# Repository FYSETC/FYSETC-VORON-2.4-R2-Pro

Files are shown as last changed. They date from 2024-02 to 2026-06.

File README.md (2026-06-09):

# FYSETC-VORON-2.4-R2-Pro



## 1. Project

This is FYSETC's project database for VORON 2.4 R2 kit, which is convenient for you to find information. Thanks for VORON Team's great work, they always design fantastic printers.

Official website:：https://vorondesign.com/voron2.4
Official Github：https://github.com/VoronDesign/Voron-2/tree/V2.4r2

In folder `Voron-2-Voron2.4` beside this README file, we make some small changes base on the VORON official material. Like change the board to Spider and others. 

## 2. Fysetc Spider 3.0 H7 Spider
The latest revision of the R2 Pro kit may contain the H7 Spider board, more information on flashing this board can be found on it's official github repository here: https://github.com/FYSETC/FYSETC-SPIDER-H7 and Wiki article here: https://wiki.fysetc.com/docs/SPIDERV3H7

## 3. Fysetc SB Combo V2
The latest revision of the R2 Pro kit may contain the SB Combo V2 Toolhead board, more information on flashing this board can be found on it's official github repository here: https://github.com/FYSETC/SB_Combo_V2/tree/main and Wiki article here: https://wiki.fysetc.com/docs/SBComboV2

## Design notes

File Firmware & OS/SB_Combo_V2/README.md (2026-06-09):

Configuration for the FYSETC-VORON-2.4-R2-Pro with Fysetc SB_Combo_V2 toolhead board.

See https://wiki.fysetc.com/docs/SBComboV2 for more info on the SB Combo V2

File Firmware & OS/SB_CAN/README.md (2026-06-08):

Config for FYSETC-VORON-2.4-R2-Pro with SB_CAN toolhead board.

1. Set Spider V3.0 to  "USB to CAN bus bridge",at the "make menuconfig" command;
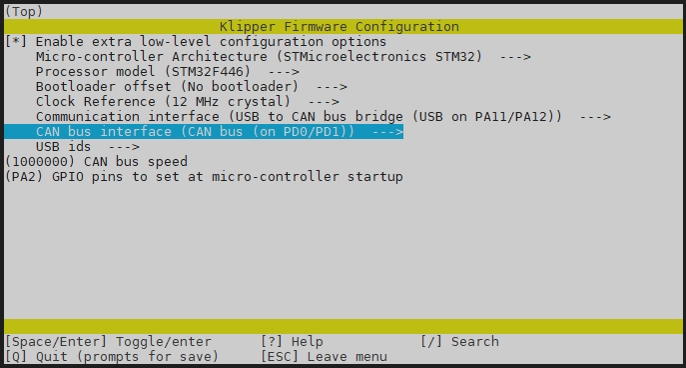
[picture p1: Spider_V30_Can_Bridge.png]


How to upload Spider V3.0 firmware?
Please refer to the following link:
https://wiki.fysetc.com/SB%20CAN%20ToolHead/#for-v13

3. Set the SB CAN V1.3 to Can bus at PB8/PB9
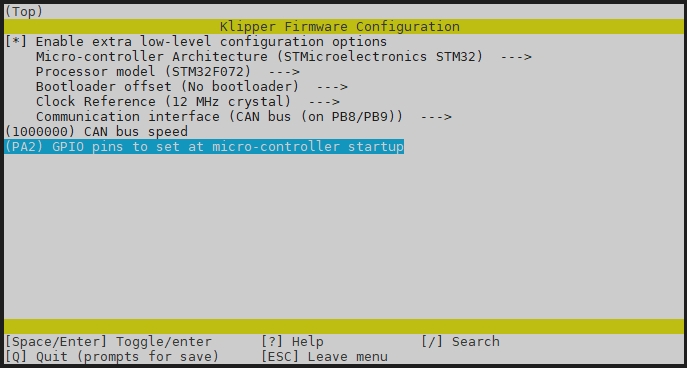
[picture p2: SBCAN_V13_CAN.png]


How to upload SB CAN V1.3 firmware?
Please refer to the following link:
https://wiki.fysetc.com/SB%20CAN%20ToolHead/#for-v13

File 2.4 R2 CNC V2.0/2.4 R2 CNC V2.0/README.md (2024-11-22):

# FYSETC-VORON-2.4-R2-Pro



## 1. Project

# VORON 2 4 R2 V2 0 Machined parts plus screws kit

Here is our video installation tutorial：

https://www.youtube.com/watch?v=xVdmxemSPT4

If you have any questions, please contact us as soon as possible

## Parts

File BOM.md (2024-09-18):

# Package list 

## VORON 2.4 R2 PRO 350 Revision 1.0

| Index | Sort | Component | Qty | Note |
| ----- | --- | --- | --- | --- |
| 1 | Fasteners | Voron V2.4 R2 fasteners Pack（12.9） | 1 SET  | |
| 2 | Motion | GATES GT2 Open Belt LL-2GT-6 (6mm wide) - 2000mm | 2 PC | |
| 3 | Motion | GATES GT2 Open Belt LL-2GT-9 (9mm wide) - 1200mm | 4 PC | |
| 4 | Motion | GATES GT2 Belt Loop (6mm W) - 188mm | 4 PCS  | |
| 5 | Motion | GT2 20T Pulley (5mm ID 6mm W) | 2 PCS  | |
| 6 | Motion | GT2 16T Pulley (5mm ID 6mm W) | 4 PCS  | |
| 7 | Motion | GT2 20T Pulley (5mm ID 9mm W) | 4 PCS  | |
| 8 | Motion | GT2 20T Toothed Idler (5mm ID 6mm W) | 2 PCS  | |
| 9 | Motion | GT2 20T Toothed Idler (5mm ID 9mm W) | 4 PCS  | |
| 10 | Motion | GT2 80T Pulley (5mm ID 6mm W) | 4 PCS  | |
| 11 | Motion | F695-2RS Bearing | 20 PCS | |
| 12 | Motion | 625 Bearing | 12 PCS | |
| 13 | Motion | 5x60mm Shaft | 4 PCS  | |
| 14 | Motion | Linear Rail MGN9H 400mm | 6 PCS  | |
| 15 | Motion | Linear Rail MGN12H Z1 400mm Light weight Stainless steel 440C | 1 PCS  | upgrade |
| 16 | Vibration Management | Rubber Compressor Foot | 4 PCS  | |
| 17 | Electronics | Stealthburner CAN Toolhead Board | 1 SET  | upgrade |
| 18 | Electronics | Stealthburner CAN Toolhead Board | 1 PC | upgrade |
| 19 | Electronics | X AXIS ENDSTOP OMRON MICROSWITCH | 1 SET  | ON extruder |
| 20 | Electronics | Y AXIS ENDSTOP OMRON MICROSWITCH | 1 SET  | Independent |
| 21 | Electronics | NeoPixel RGBW Mini Button PCB LED | 1 SET  | upgrade |
| 22 | Electronics | Omron G3NB-225B-1 SSR | 1 PC | |
| 23 | Electronics | NEMA17 Motor  17HS19-2004S-C (check [here](https://github.com/FYSETC/FYSETC-MOTORS/tree/main/17HS19-2004S-C)) | 4 PCS  | |
| 24 | Electronics | NEMA17 Motor  17HS19-2004S-AB (XY motor check [here](https://github.com/FYSETC/FYSETC-VORON-2.4-R2-Pro/tree/main/Docs/Stepper%20motor%20parameters)) | 2 PCS  | upgrade |
| 25 | Electronics | G36HSY4405-6D-60(check [here](https://github.com/FYSETC/FYSETC-VORON-2.4-R2-Pro/tree/main/Docs/Stepper%20motor%20parameters)) | 1 PC | |
| 26 | Electronics | Mean Well LRS-200-24 PSU | 1 PC | |
| 27 | Electronics | Inlet Power Socket CW2B-10A-T | 1 SET  | upgrade |
| 28 | Electronics | 40x40x10 Axial Fan (24V)  Dual Ball Bearing | 1 PC | upgrade |
| 29 | Electronics | 50x50x15 Centrifugal Fan (24V)  Dual Ball Bearing | 1 PC | upgrade |
| 30 | Electronics | 60x60x20 Fan (24V)kit（3 PCS）Dual Ball Bearing | 1 SET  | upgrade |
| 31 | Electronics | Keystone CAT6 Insert | 1 PC | |
| 32 | Electronics | C13 Power Cord | 1 PC | |
| 33 | Controller | RaspberryPi（Optional） | 1 PC | |
| 34 | Controller | sdcard 16GB | 1 PC | |
| 35 | Controller | USB C cable | 1 PC | |
| 36 | Controller | SPIDER_H7_V30 Board | 1 PC | |
| 37 | Controller | TMC2209 Stepper Motor Driver | 6 PCS  | |
| 38 | Controller | HDMI5 Display | 1 PC | upgrade |
| 39 | Frame | Light weight Gantry | 1 SET  | upgrade |
| 40 | Frame | OpenBuilds Angle Corner Connector | 4 PCS  | |
| 41 | Frame | Misumi sectional profile Kit HFSB5-2020 SET | 18 PCS | |
| 42 | Misc | PTFE Tube (4mm OD 2mm ID) - 1.5m | 1 PC | |
| 43 | Misc | 6x3mm Neodimium Magnet | 10 PCS | |
| 44 | Misc | 4mm Bowden Coupler | 1 PC | |
| 45 | Misc | BMG nano-coating one-piece helical gear kit (Includes all accessories) | 1 SET  | upgrade |
| 46 | Misc | Sailfish High Flow Hotend （ all-metal hotend 24V 60W) | 1 SET  | upgrade |
| 47 | Misc | DIN 3 Rails (35mm W) - 460mm | 2 PCS  | |
| 48 | Misc | DIN Rail Mount Bracket for G3A SSR | 1 PC | |
| 49 | Misc | Fume Extractor Carbon Filter Element | 1 PC | |
| 50 | Misc | 3M VHB Tape 5952 | 1 PC | |
| 51 | Misc | Foam Tape Thickness 1mm Length 5m | 1PC | |
| 52 | Misc | Foam Tape Thickness 3mm Length 4m | 2 PCS  | |
| 53 | Misc | XH2.54 2/3/4 Pin Plastic shell | 1 SET  | |
| 54 | Mics | Zip ties | 1 SET  | |
| 55 | Cables | Cable Kit（Pre-crimped terminals and longer wire lengths with label） | 1 SET  | |
| 56 | Cables | VORON 2.4 Chain Kit (1PC 15X10mm，XY axis cancellation) | 1 PC | Change |
| 57 | Panels | Bottom/Back/Electronics Bay Panels | 3 PCS  | |
| 58 | Panels | Side/Front/Top Acrylic Panels | 4 PCS  | |
| 59 | Buildplate | MIC6 5/16" Plate - 355X355mm （Surface milling improve flatness） | 1 PC | |
| 60 | Buildplate | Silicone AC Heater - 350x350mm (1000W)+Thermal Fuse RH15A125（Pluggable） | 1 PC | upgrade |
| 61 | Buildplate | JanusBPS Textured steel plate 355X355mm （One side pattern and the other side glossy PEI sticker） | 1 PC | [JanusBPS](https://www.google.com/search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) |
| 62 | Buildplate | Scratch-proof Magnetic stickers 355X355mm thickness 1.5mm | 1 PC | upgrade |
| 63 | Buildplate | Hotbed Insulation cotton thickness 5mm | 1 PC | upgrade |
| 64 | Tool | Cutting pliers | 1 PC | |
| 65 | Tool | Hexagonal wrenchs | 1 SET  | |
| 66 | Tool | Thermal silica | 1 PC | |
| 67 | Mics | PVC wiring duct 30x30mm | 1 SET  | |
| 68 | Mics | Wago 221-415 Terminals | 3 PCS  | |
| 69 | Mics | VORON Nevermore V6 | 1 SET  | upgrade |
| 70 | Mics | Weaving casing | 1 SET  | |
| 71 | Mics | The standby line 3m | 1 PC | |
| 72 | Mics | Wiring diagram | 1 PC | |
| 73 | Mics | VORON Hotend Cleaning brush | 1 SET  | upgrade |
| 74 | Mics | VORON Hotbed PEEK column | 1 SET  | upgrade |
| 75 | Mics | VORON CNC TAP Aluminium alloy（HIWIN） | 1 SET  | upgrade |

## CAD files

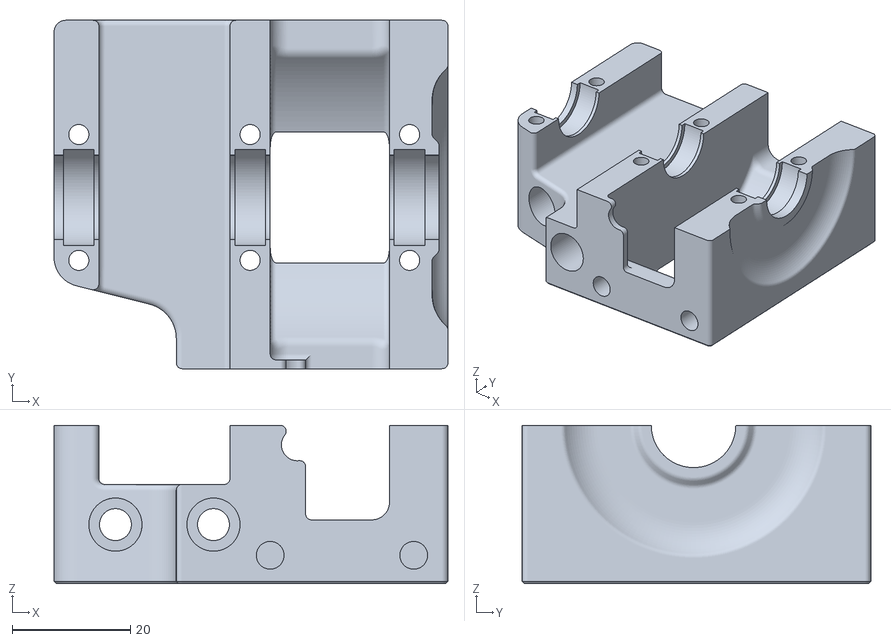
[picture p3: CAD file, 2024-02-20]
STLs/Z_Drive/z_drive_main_b_x2.stl
66.7 x 59.0 x 26.8

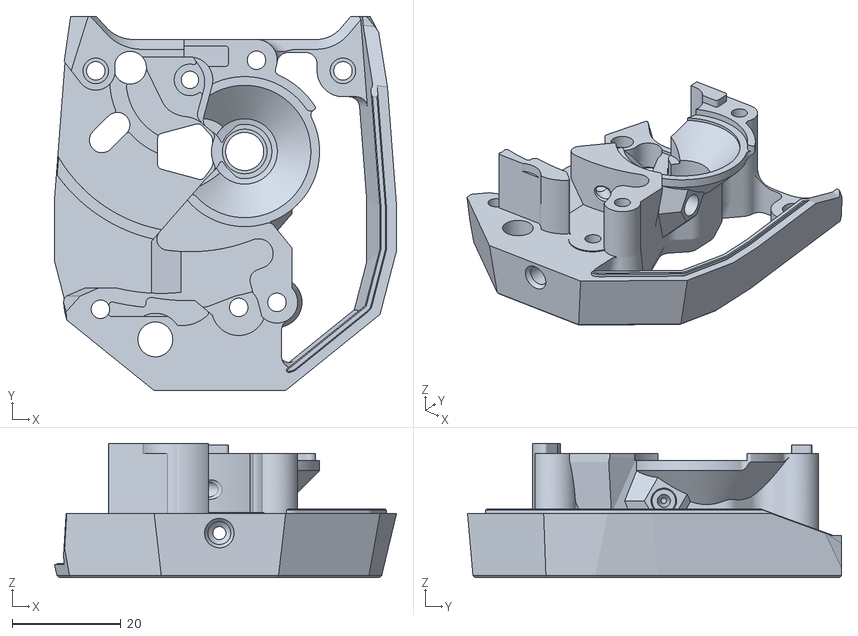
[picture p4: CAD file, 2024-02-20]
2.4 R2 CNC V2.0/2.4 R2 CNC V2.0/STL/VORON 2.4 R2 350 size V2.0 CNC SLT file/Gantry/X_Axis/X_Carriage/Voron-Stealthburner/Clockwork2/Direct_Drive/main_body.stl
62.8 x 68.7 x 24.7

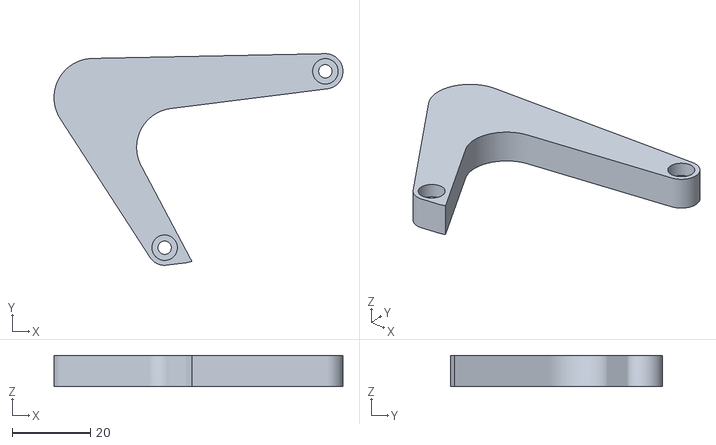
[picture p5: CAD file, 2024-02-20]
2.4 R2 CNC V2.0/2.4 R2 CNC V2.0/STL/VORON 2.4 R2 300 size V2.0 CNC SLT file/Skirts/HDMI5 Display/Five inches-Main arm B x1.STL
73.7 x 54.0 x 8.00

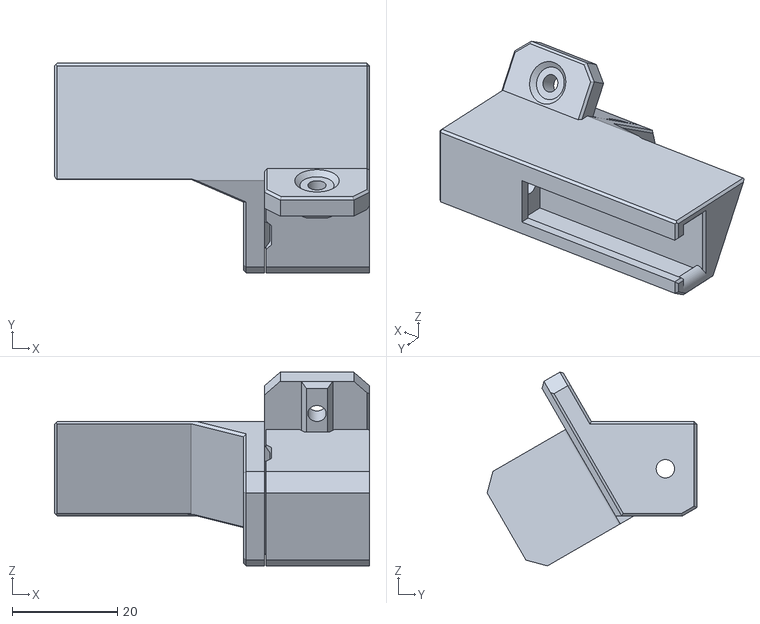
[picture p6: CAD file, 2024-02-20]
2.4 R2 CNC V2.0/2.4 R2 CNC V2.0/STL/VORON 2.4 R2 300 size V2.0 CNC SLT file/Cleaning brush/Voron R2&2.4 Cleaning brush.STL
60.0 x 39.9 x 36.9

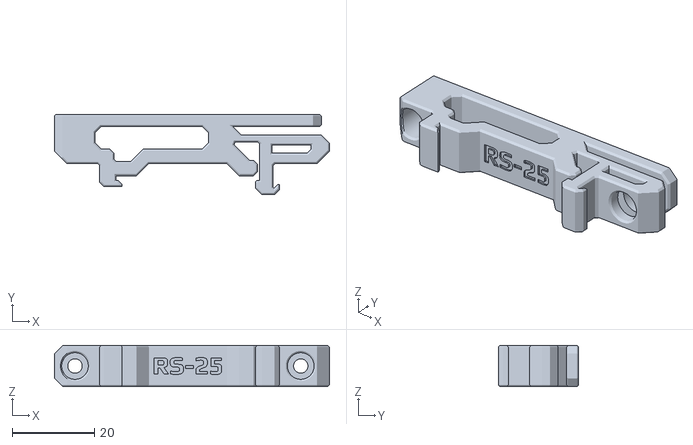
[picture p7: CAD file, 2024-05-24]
2.4 R2 CNC V2.0/2.4 R2 CNC V2.0/STL/VORON 2.4 R2 300 size V2.0 CNC SLT file/Electronics_Bay/rs25_psu_bracket.stl
67.0 x 19.6 x 10.0

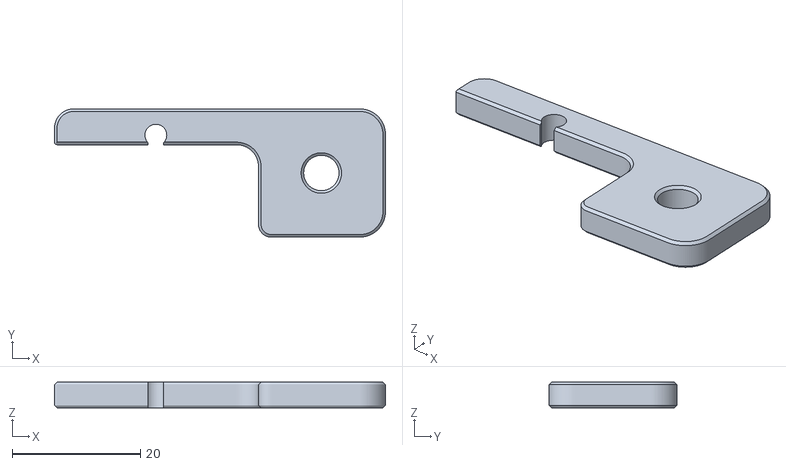
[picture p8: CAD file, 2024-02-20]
2.4 R2 CNC V2.0/2.4 R2 CNC V2.0/STL/VORON 2.4 R2 300 size V2.0 CNC SLT file/Exhaust_Filter/[a]_exhaust_filter_mount_x2.stl
51.6 x 20.0 x 4.00

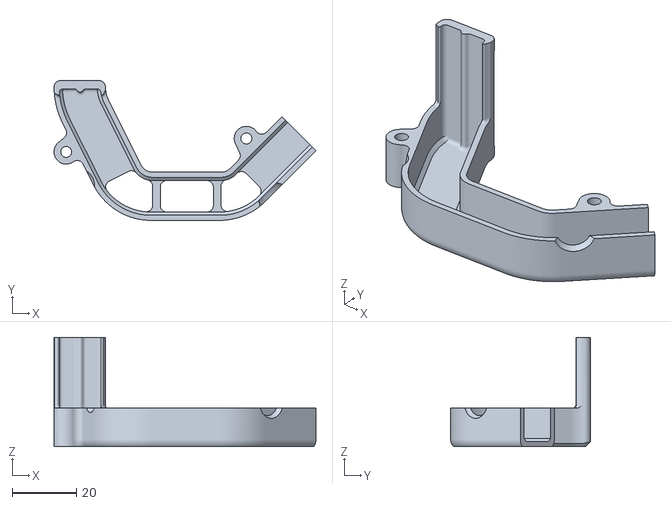
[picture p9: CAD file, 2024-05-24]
2.4 R2 CNC V2.0/2.4 R2 CNC V2.0/STL/VORON 2.4 R2 300 size V2.0 CNC SLT file/Gantry/AB_Drive_Units/[a]_cable_cover.stl
81.5 x 43.5 x 34.0

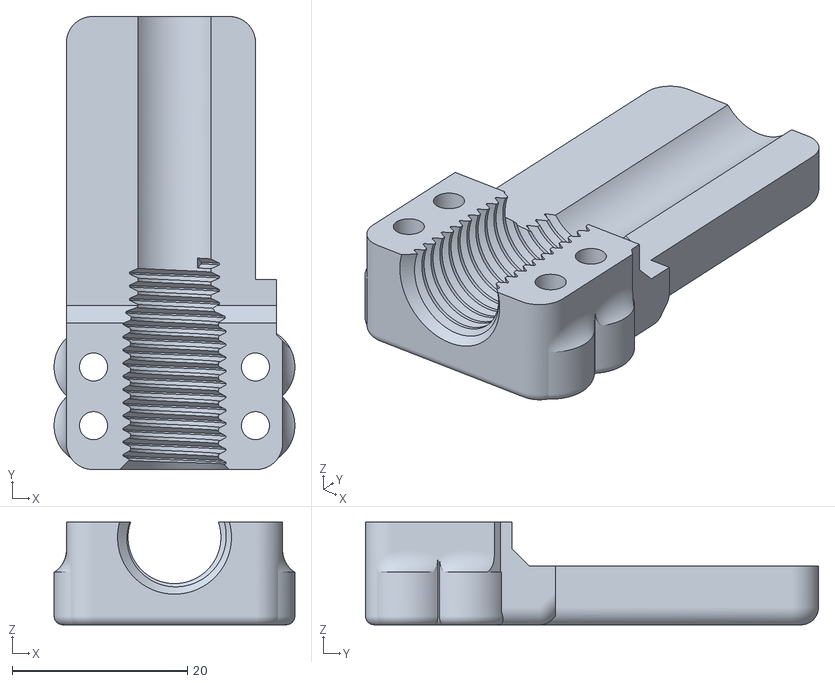
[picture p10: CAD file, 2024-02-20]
2.4 R2 CNC V2.0/2.4 R2 CNC V2.0/STL/VORON 2.4 R2 300 size V2.0 CNC SLT file/Gantry/AB_Drive_Units/Rear_Umbilical/front_cover.STL
27.5 x 51.7 x 11.7

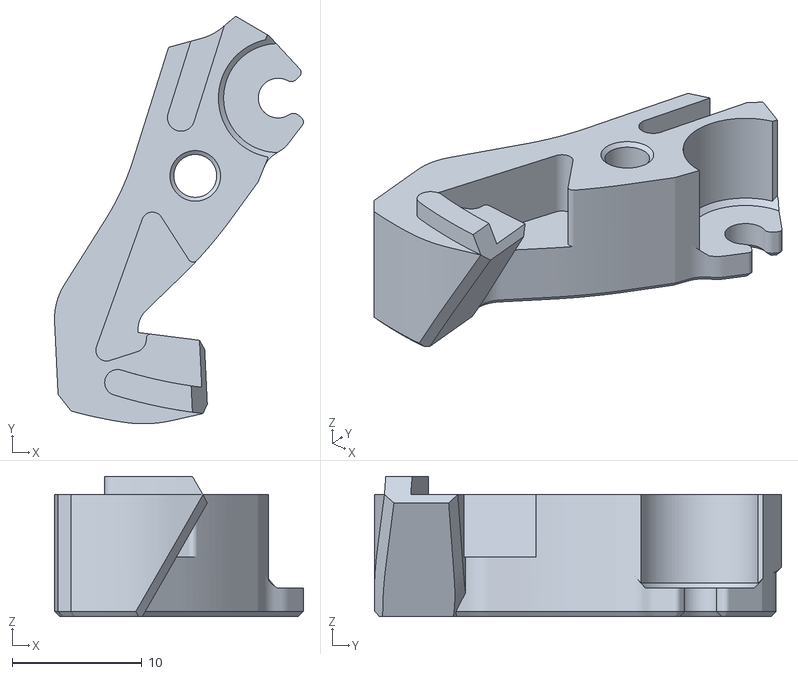
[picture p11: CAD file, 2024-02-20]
2.4 R2 CNC V2.0/2.4 R2 CNC V2.0/STL/VORON 2.4 R2 300 size V2.0 CNC SLT file/Gantry/X_Axis/X_Carriage/Voron-Stealthburner/Clockwork2/Direct_Drive/[a]_guidler_b.stl
19.2 x 31.4 x 10.8

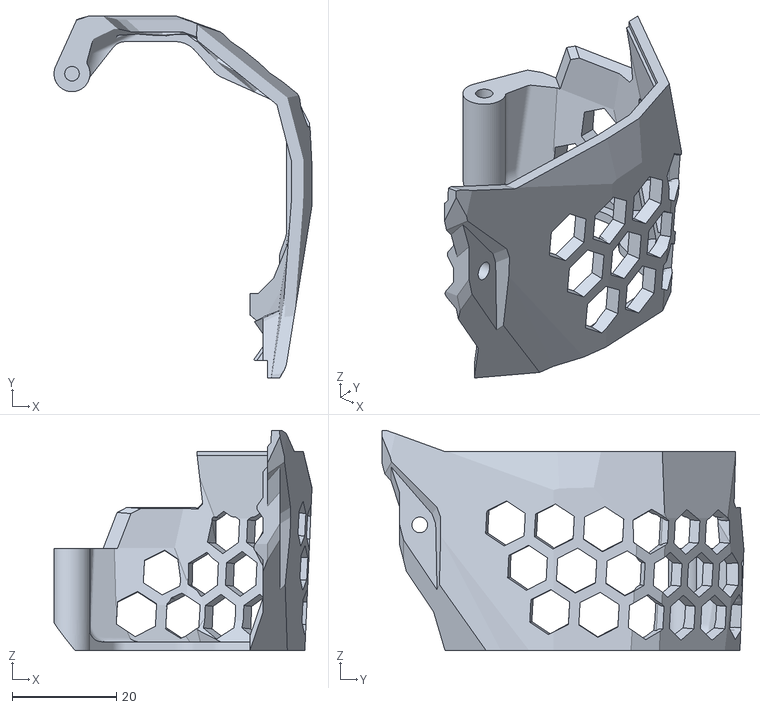
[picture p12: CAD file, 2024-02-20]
2.4 R2 CNC V2.0/2.4 R2 CNC V2.0/STL/VORON 2.4 R2 300 size V2.0 CNC SLT file/Gantry/X_Axis/X_Carriage/Voron-Stealthburner/Clockwork2/light_weight_cable_door_for_pcb.stl
49.5 x 69.4 x 42.2

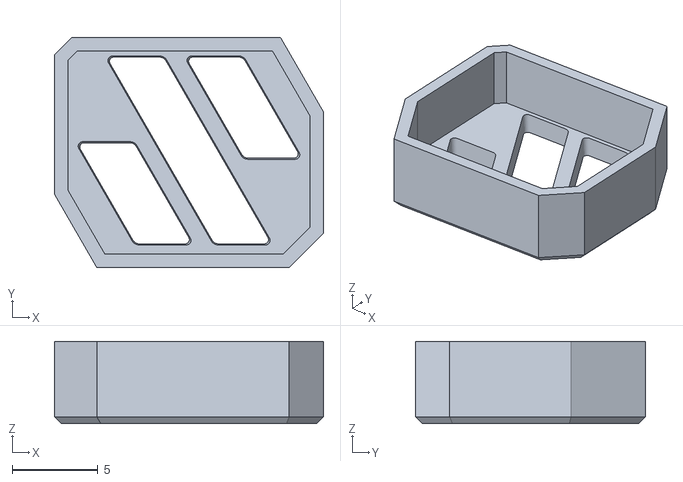
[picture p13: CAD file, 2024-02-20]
2.4 R2 CNC V2.0/2.4 R2 CNC V2.0/STL/VORON 2.4 R2 300 size V2.0 CNC SLT file/Gantry/X_Axis/X_Carriage/Voron-Stealthburner/Stealthburner/[o]_stealthburner_LED_diffuser_mask.stl
15.7 x 13.4 x 4.80

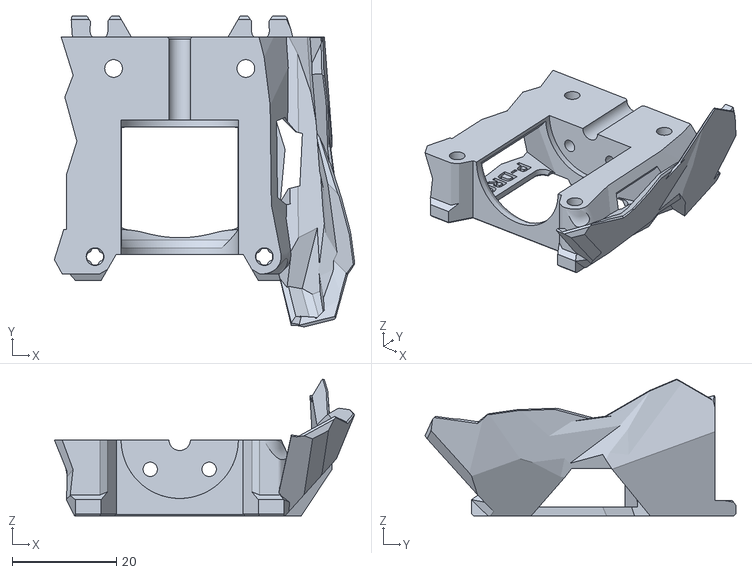
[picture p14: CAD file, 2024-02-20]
2.4 R2 CNC V2.0/2.4 R2 CNC V2.0/STL/VORON 2.4 R2 300 size V2.0 CNC SLT file/Gantry/X_Axis/X_Carriage/Voron-Stealthburner/Stealthburner/Printheads/phaetus_dragon/stealthburner_printhead_dragon_rear_cw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
57.7 x 59.7 x 26.3

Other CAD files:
CAD/CAD/VORON2.4_R2_PRO_Assembly.STEP
STLs/Z_Drive/z_drive_main_a_x2.stl
2.4 R2 CNC V2.0/2.4 R2 CNC V2.0/STL/VORON 2.4 R2 300 size V2.0 CNC SLT file/Skirts/HDMI5 Display/Five inches-Main arm A x1.STL
2.4 R2 CNC V2.0/2.4 R2 CNC V2.0/STL/VORON 2.4 R2 350 size V2.0 CNC SLT file/Skirts/HDMI5 Display/Five inches-Main arm A x1.STL
2.4 R2 CNC V2.0/2.4 R2 CNC V2.0/STL/VORON 2.4 R2 300 size V2.0 CNC SLT file/Electronics_Bay/PSU_stabilizer_50mm.stl
2.4 R2 CNC V2.0/2.4 R2 CNC V2.0/STL/VORON 2.4 R2 300 size V2.0 CNC SLT file/Electronics_Bay/Spider_bracket_set.stl
2.4 R2 CNC V2.0/2.4 R2 CNC V2.0/STL/VORON 2.4 R2 300 size V2.0 CNC SLT file/Electronics_Bay/lrs_200_psu_bracket_x2.stl
2.4 R2 CNC V2.0/2.4 R2 CNC V2.0/STL/VORON 2.4 R2 300 size V2.0 CNC SLT file/Electronics_Bay/pcb_din_clip_x3.stl
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

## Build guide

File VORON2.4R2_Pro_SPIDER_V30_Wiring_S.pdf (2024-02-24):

L1 L3 L1 | N1PE1 | GND Bed L | G2 G1 V1V2 V1 V2G1 G2 | Z2 | A | B Z1 | Z0 Exhaust Fan(EF) Z0 | Z2 Z1 | Ymin ControllerFan(CF) | TB HDMI5 Display | ControllerFan(CF) Relay Signal (RS) | Relay Signal(RS) | FYSETC Voron 2.4 R2 Pro kit Wring example | - by George Fu Docs Find kit details(corresponding firmware, printer.cfg, specific printed parts, etc.) on our github: https://github.com/FYSETC/FYSETC- VORON-2.4-R2-Pro Note 1: All cables have label on, do wiring according to the label shows. Note 2: The cable with the labels below are on extruder cable harness.They are used to connect CAN PCB. X, A, B,HF, CF, E Note 3: USBC cable is optional if you use UART to communicate with Raspi, github : https://github.com/FYSETC/FYSETC- SPIDER/blob/main/firmware/Klipper/Con nect%20RPI%20uart.md Note 4: Check your fan voltage jumpers, all fans in the kit are 24v. Note 5: Wango connectors are included in kit, it is useful when you want to add 5V PSU. But we did not use it on this wiring example. Note 6: The power inlet cord color may different from kit one. Stick to the labels. Note 7: Make sure you have appropriate tools, you may be able to rent some equipment from your local hardware store. Note 8: Use multimeter to test connection after you finish wiring. Note 9: Check the input voltage switch of the power supply. It is located in the highlighted area behind the metal mesh. Make sure the selection matches your local mains voltage. Recommend to do power supply wiring and test it first before you wire other parts. Note 10: Make sure the power is off at the breaker before you start and use a voltage tester to verify that. Make sure wires and/or electrical connections are completely dead before you start working on them. Make sure everyone in your home is aware that electrical work is going on. Tape the circuit breaker into the off position. Z3 | Z3 CAN GND 24V Nevermore Fan RaspberryPI cable | RaspberryPI cable PE1 | N1 L3 Bed N Bed PE(BPE) USBC | USBC 2 | 1 3 | 4 | CAN L CAN H HDMI5 Display cable | Why is it slanted? Don't learn from me, it's stuck crooked. ^V^

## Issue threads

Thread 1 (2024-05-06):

5 inches lcd case

Karolas123, 2024-05-06:
Can you paste the instructions on how to assemble the elements of the 5-inch LCD housing?

Hoganzen, 2024-05-24:
Please refer to it.
https://www.youtube.com/watch?v=sUrsYsw5mUA

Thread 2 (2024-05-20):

Would it be possible for you to make the Voron 2.4 Pro CAD model available for us to download?

VitorOM, 2024-05-20:
Would it be possible for you to make the Voron 2.4 Pro CAD model available for us to download?

@Hoganzen
@RichardTHF
@eliwong

As it is a different model from the original Voron 2.4, it would be of great help in assembly and modifications.

VitorOM, 2024-05-28:
> Hello, I have uploaded the CAD file.

Thanks a lot!

Closed 2024-05-26.

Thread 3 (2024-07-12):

Cannot find tutorial for CNC Parts Kit V2.0

VORONENTHUSIAST, 2024-07-12:
I bought your CNC V2.0 Parts Kit from Aliexpress - it said there was a tutorial to follow for installation, where is it?

Thanks

jinhong-, 2024-07-13:
Heya, i am not sure if there is a different 2.0 CNC kit but this is the one i followed
https://www.youtube.com/watch?v=xVdmxemSPT4

YoungHillionaire, 2024-07-25:
it does not show how to install the z drive joints
documentation are lacking and very poor

VORONENTHUSIAST, 2024-07-25:
> Heya, i am not sure if there is a different 2.0 CNC kit but this is the one i followed https://www.youtube.com/watch?v=xVdmxemSPT4

Thanks that really helped actually! I've left it sat for a few days due to work and everything but only have the Z drive units left to go, everything else is built and installed on the printer.

> it does not show how to install the z drive joints documentation are lacking and very poor

From looking at the Z drive units, you don't need a tutorial for those...

Grpwomble, 2024-08-24:
i’ve been searching for four days and even contacted the manufacturer. This video is exactly what I have. Thank you so much. Saved me a headache. It’s perfect and thank you again.

hensenx, 2024-09-01:
Add this link (and lcd video as well) to readme.md, since this is the repository you're sharing with customers. Makes for a much better experience!

Closed 2024-09-08.

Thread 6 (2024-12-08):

hollow CNC X gantry fixed block is missing!

radpod, 2024-12-08:
I got a VORON 2.4 R2 Pro with nice CNC X gantry, but it requires use of fixed blocks as the holes have no thread.
This file is not available to print, at least I could not find it and there is not instruction either.
This is a big stop while making the assembly.
Please, fix this.

ntrp, 2025-02-15:
Just in case somebody stumbles on this https://github.com/FYSETC/FYSETC-VORON-2.4-R2-Pro/blob/main/STLs/Gantry/X_Axis/XY_Joints/Lightweight%20Gantry%20fixed%20x2.STL

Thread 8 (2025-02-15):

Flash configuration wrong

ntrp, 2025-02-15:
The flash configurations in SBCAN_v13_CAN.jpg are duplicated and both of them are partially wrong..

One is showing 12Mhz crystal and the other is showing STM32G0B1..

The correct configuration is:
- STM32F072
- No Bootloader
- 8Mhz crystal
- Communication interface (CAN bus (on PB8/PB9))

Please leave only one image with the correct values, it wasted me already hours of work over a couple of times..

valo, 2025-04-11:
Just noticed this issue. Good that I had trouble putting the board in DFU mode and went over the whole internet to learn everything about this board. Pls, update the screenshot so that ppl don't get in trouble flashing with the wrong config.

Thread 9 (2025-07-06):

No X Carriage .STL available (NON TAP) I bought the entire printed parts kit and i am scammed by Evelien Zang and Michael

MXSPIBE, 2025-07-06:
The X-Carriage is not included in the complete printed parts kit, no CAD/STEP or STL file found ony redirections?
Complete means COMPLETE.
Meanwhile i am about to finish the build and this again another big bummer.

Thanks
Kind Regards,
Marnix Simons
Belgium.

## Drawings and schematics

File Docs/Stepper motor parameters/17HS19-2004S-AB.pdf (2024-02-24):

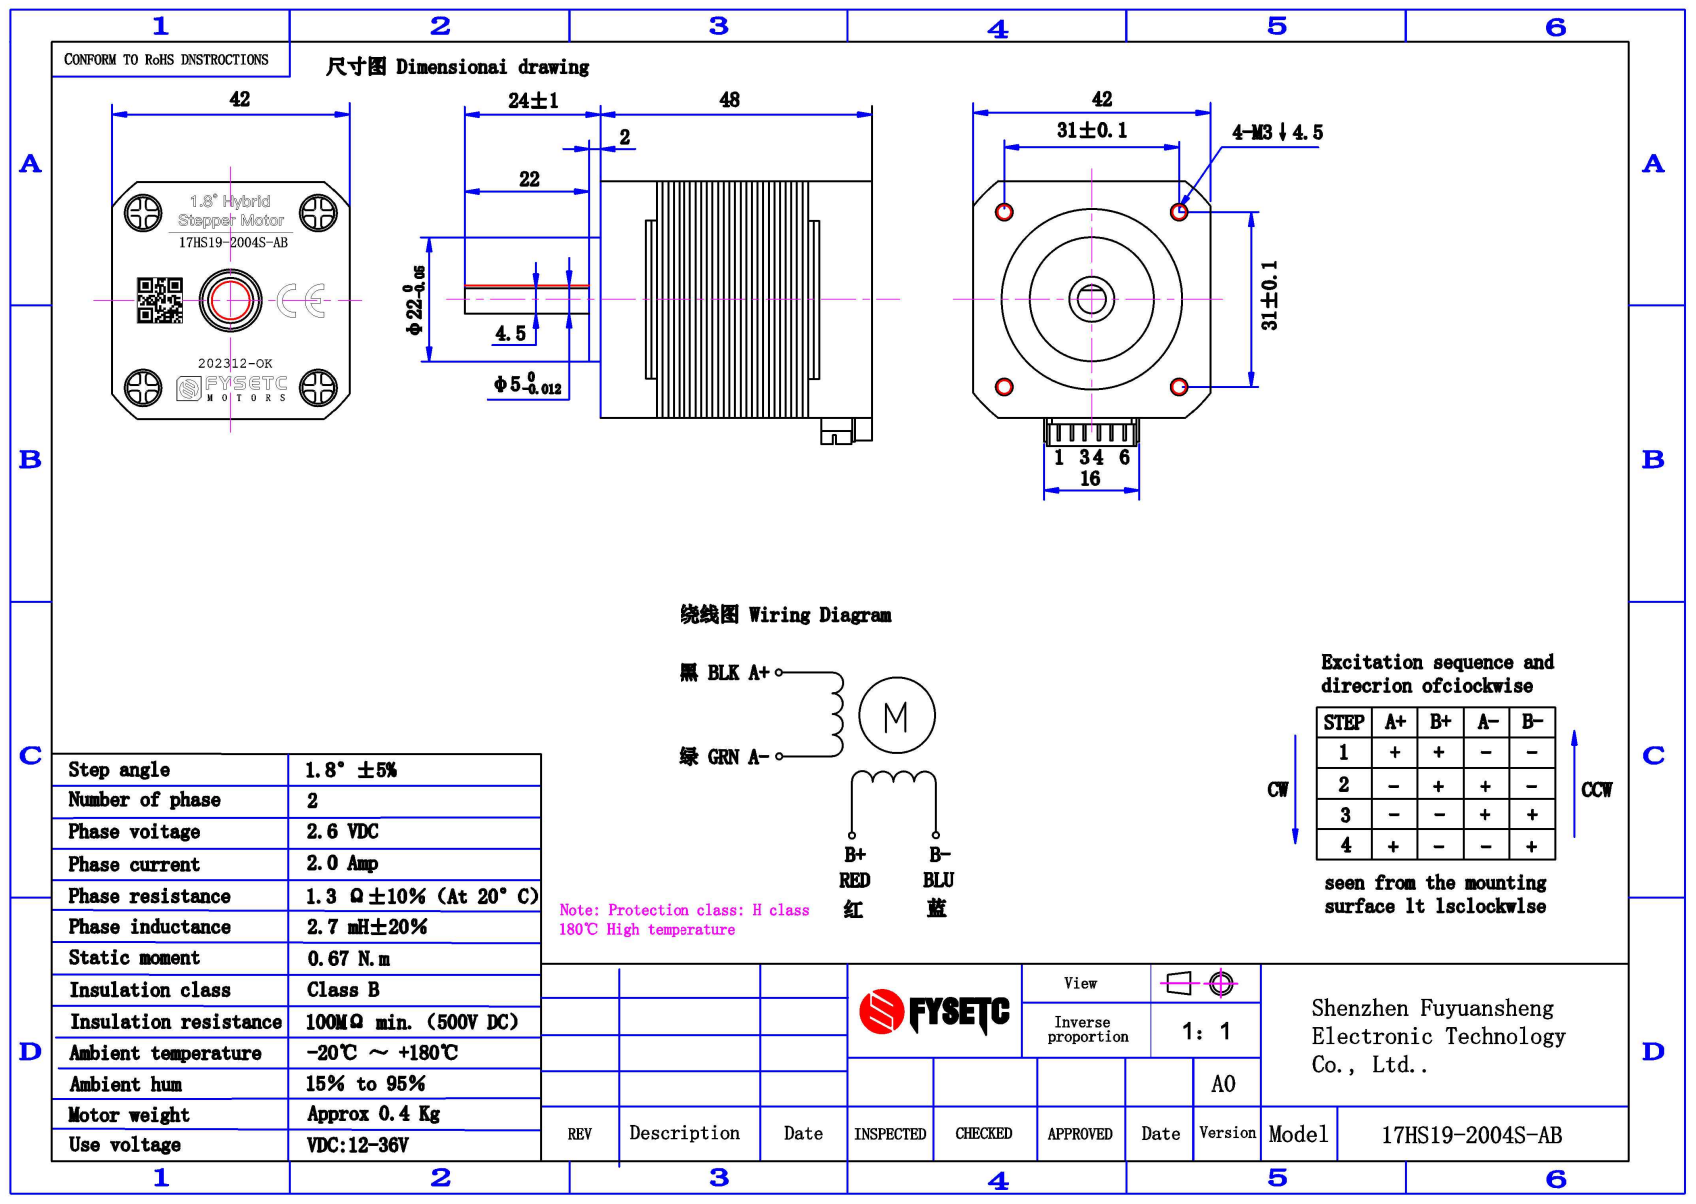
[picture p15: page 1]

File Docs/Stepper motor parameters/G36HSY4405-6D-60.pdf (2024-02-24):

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

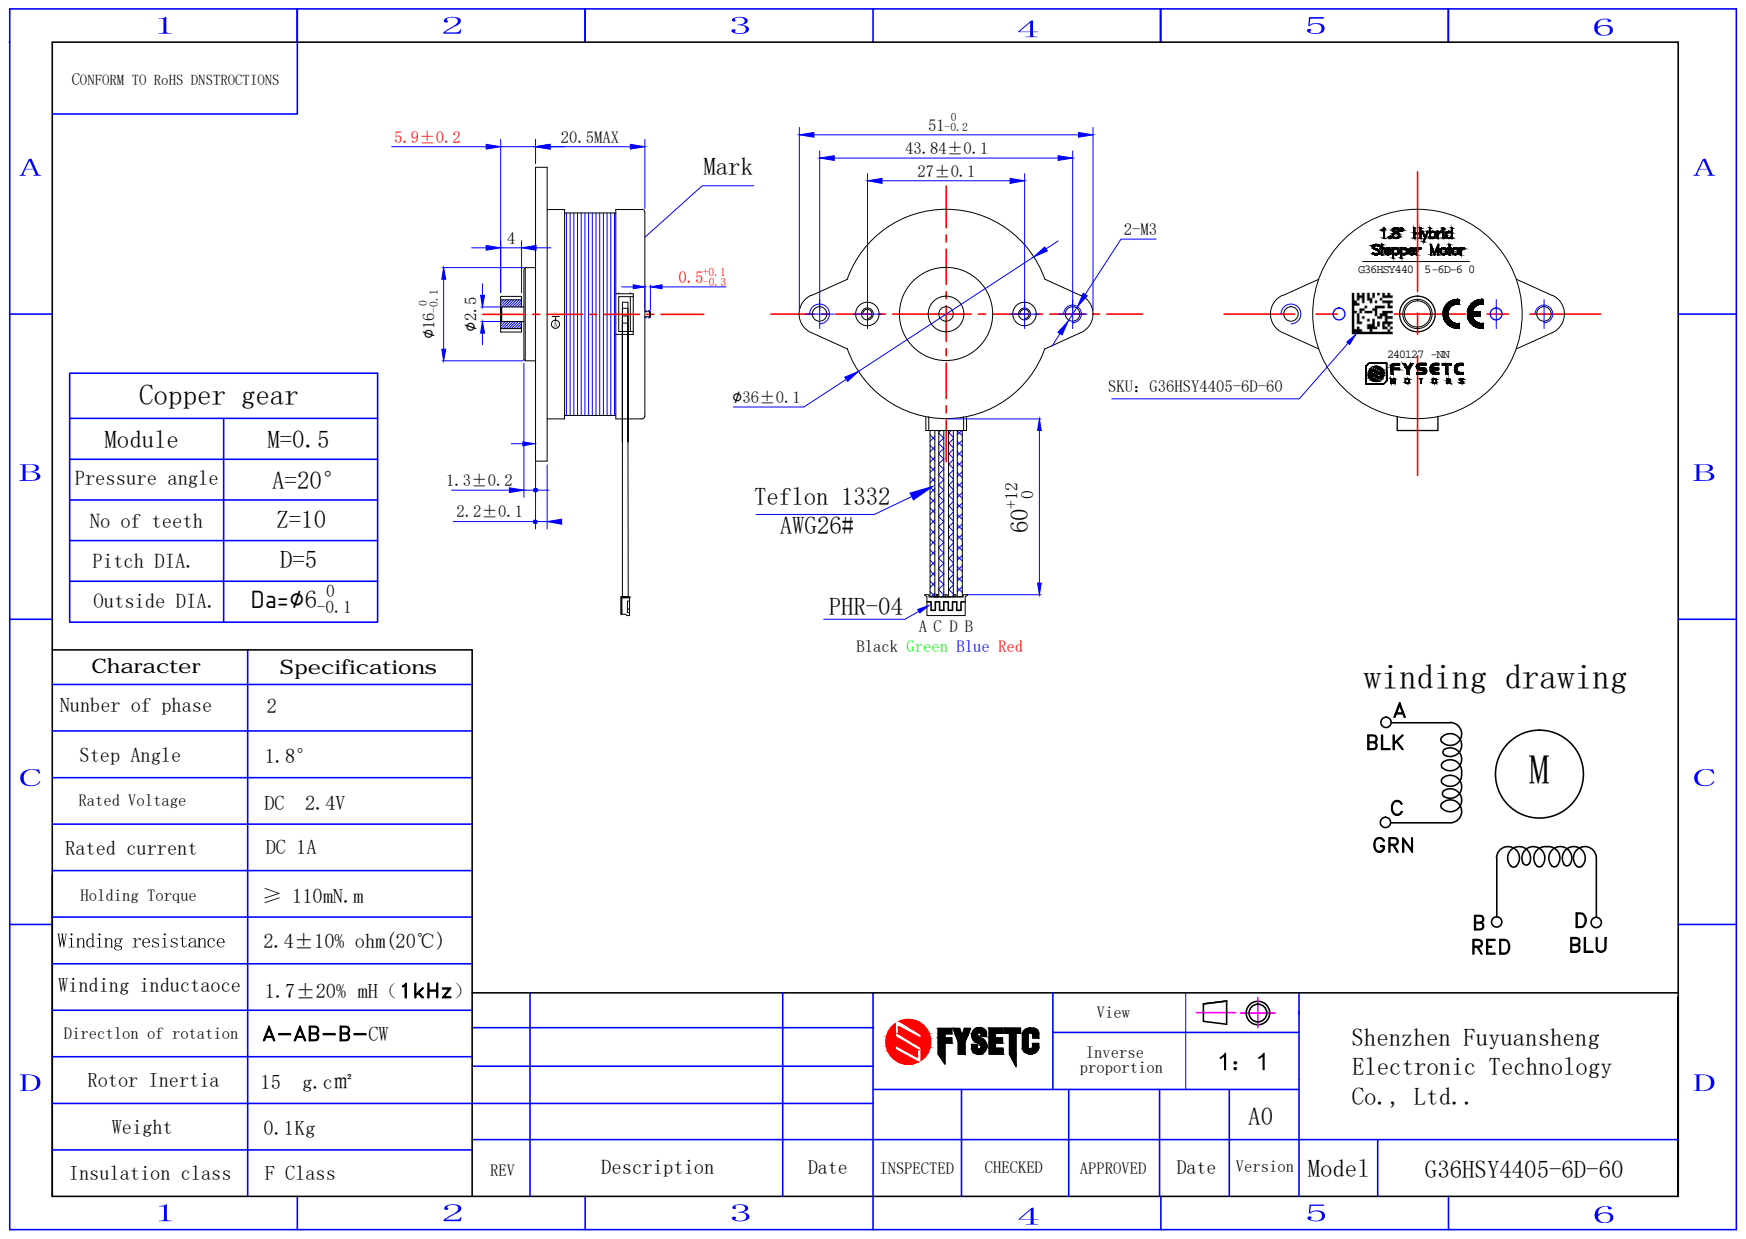
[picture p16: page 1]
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

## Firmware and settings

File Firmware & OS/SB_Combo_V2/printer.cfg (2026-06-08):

# See docs/Config_Reference.md for a description of parameters.

## Voron Design VORON2 250/300/350mm Spider TMC2209 UART config

## *** THINGS TO CHANGE/CHECK: ***
## MCU paths							[mcu] section
## Thermistor types						[extruder] and [heater_bed] sections - See 'sensor types' list at end of file
## Z Endstop Switch location			[safe_z_home] section
## Homing end position                  [gcode_macro G32] section
## Z Endstop Switch  offset for Z0		[stepper_z] section
## Probe points							[quad_gantry_level] section
## Min & Max gantry corner postions		[quad_gantry_level] section
## PID tune								[extruder] and [heater_bed] sections
## Fine tune E steps					[extruder] section
[include mainsail.cfg]

[printer]
kinematics: corexy
max_velocity: 500  
max_accel: 6000			        #Max 4000
max_z_velocity: 15				#Max 15 for 12V TMC Drivers, can increase for 24V
max_z_accel: 350
square_corner_velocity: 5.0


[mcu]
##  You need to select 'Communication interface' to USB in 'make menuconfig'
##  when you compile Klipper for Spider
##	Obtain definition by "ls -l /dev/serial/by-id/" then unplug to verify
##--------------------------------------------------------------------
#serial: /dev/serial/by-id/usb-Klipper_stm32f446xx_230032000851363131363530-if00

##	If you want to use the Raspberry uart0 to communicate with Spider, 
##  you need to select 'Communication interface' to 'Serial (on USART1 PA10/PA9)' 
##  in 'make menuconfig' when you compile klipper and set the serial as below
##--------------------------------------------------------------------
#serial: /dev/ttyAMA0
## Uncomment below if you're using the Raspberry uart0 to communicate with Spider
#restart_method: command

##--------------------------------------------------------------------
## If you want to use Spider as USB to CAN bridge,you need to select 
## 'Communication interface' to 'USB to CAN bus bridge (USB on PA11/PA12)' 
##  in 'make menuconfig' when you compile klipper and follow the instruction on
## klipper docs to set the canbus id : http://www.klipper3d.org/CANBUS.html?h=can
##--------------------------------------------------------------------
canbus_uuid=YOURUUID


## Below is the config for SB CAN TH, copy from sb_can_th.cfg
## https://github.com/FYSETC/FYSETC_SB_CAN_TOOLHEAD/blob/main/sb_can_th.cfg
[mcu sb_can_th]
# Follow the instruction here https://www.klipper3d.org/CANBUS.html to get CAN id
canbus_uuid=YOURUUID

[adxl345]
cs_pin: sb_can_th:PB12
spi_software_sclk_pin: sb_can_th:PB13
spi_software_mosi_pin: sb_can_th:PB15
spi_software_miso_pin: sb_can_th:PB14
axes_map: -y,z,-x

[resonance_tester]
accel_chip: adxl345
probe_points:
    175,175,30 # an example
	
#####################################################################
#      X/Y Stepper Settings
#####################################################################

[stepper_x]
##	Connected to X-MOT (B Motor)
step_pin: PE11
dir_pin: PE10
enable_pin: !PE9
rotation_distance: 40
microsteps: 16
full_steps_per_rotation:200  #set to 400 for 0.9 degree stepper
endstop_pin: sb_can_th:PA2 #^PB14
position_min: 0

##--------------------------------------------------------------------

##	Uncomment below for 250mm build
#position_endstop: 250
#position_max: 250

##	Uncomment for 300mm build
#position_endstop: 300
#position_max: 300

##	Uncomment for 350mm build
position_endstop: 350
position_max: 350

##--------------------------------------------------------------------
homing_speed: 25   #Max 100
homing_retract_dist: 5
homing_positive_dir: true

##	Make sure to update below for your relevant driver (2208 or 2209)
[tmc2209 stepper_x]
uart_pin: PE7
interpolate: True
run_current: 1.0
hold_current: 0.7
sense_resistor: 0.110
stealthchop_threshold: 0

[stepper_y]
##	Connected to Y-MOT (A Motor)
step_pin: PD8
dir_pin: PB12
enable_pin: !PD9
rotation_distance: 40
microsteps: 16
full_steps_per_rotation:200  #set to 400 for 0.9 degree stepper
endstop_pin: ^PB13
position_min: 0
##--------------------------------------------------------------------

##	Uncomment for 250mm build
#position_endstop: 250
#position_max: 250

##	Uncomment for 300mm build
#position_endstop: 305
#position_max: 305

##	Uncomment for 350mm build
position_endstop: 350
position_max: 350

##--------------------------------------------------------------------
homing_speed: 25  #Max 100
homing_retract_dist: 5
homing_positive_dir: true

##	Make sure to update below for your relevant driver (2208 or 2209)
[tmc2209 stepper_y]
uart_pin: PE15
interpolate: True
run_current: 1.0
hold_current: 0.7
sense_resistor: 0.110
stealthchop_threshold: 0

#####################################################################
#   Z Stepper Settings
#####################################################################

## In Z-MOT Position
## Z0 Stepper - Front Left
[stepper_z]
step_pin: PD14
dir_pin: PD13
enable_pin: !PD15
rotation_distance: 40
gear_ratio: 80:16
microsteps: 16
##  In Z- Position
endstop_pin: probe:z_virtual_endstop #^PA0
##  Z-position of nozzle (in mm) to z-endstop trigger point relative to print surface (Z0)
##  (+) value = endstop above Z0, (-) value = endstop below
##	Increasing position_endstop brings nozzle closer to the bed
##  After you run Z_ENDSTOP_CALIBRATE, position_endstop will be stored at the very end of your config
#position_endstop: -0.2
##--------------------------------------------------------------------

##	Uncomment below for 250mm build
#position_max: 240

##	Uncomment below for 300mm build
#position_max: 290

##	Uncomment below for 350mm build
position_max: 340

##--------------------------------------------------------------------
position_min: -5
homing_speed: 8
second_homing_speed: 3
homing_retract_dist: 3

##	Make sure to update below for your relevant driver (2208 or 2209)
[tmc2209 stepper_z]
uart_pin: PD10
uart_address: 0
interpolate: True
run_current: 1.0
hold_current: 0.8
sense_resistor: 0.110
stealthchop_threshold: 0

##	In E1-MOT Position
##	Z1 Stepper - Rear Left
[stepper_z1]
step_pin: PE6
dir_pin: !PC13
enable_pin: !PE5
rotation_distance: 40
gear_ratio: 80:16
microsteps: 16

##	Make sure to update below for your relevant driver (2208 or 2209)
[tmc2209 stepper_z1]
uart_pin: PC14
interpolate: True
run_current: 0.8
hold_current: 0.8
sense_resistor: 0.110
stealthchop_threshold: 0

##	In E2-MOT Position
##	Z2 Stepper - Rear Right
[stepper_z2]
step_pin: PE2
dir_pin: PE4
enable_pin: !PE3
rotation_distance: 40
gear_ratio: 80:16
microsteps: 16

##	Make sure to update below for your relevant driver (2208 or 2209)
[tmc2209 stepper_z2]
uart_pin: PC15
interpolate: true
run_current: 0.8
hold_current: 0.8
sense_resistor: 0.110
stealthchop_threshold: 0

##	In E3-MOT Position
##	Z3 Stepper - Front Right
[stepper_z3]
step_pin: PD12
dir_pin: !PC4
enable_pin: !PE8
rotation_distance: 40
gear_ratio: 80:16
microsteps: 16

[tmc2209 stepper_z3]
uart_pin: PA15
interpolate: true
run_current: 0.8
hold_current: 0.8
sense_resistor: 0.110
stealthchop_threshold: 0

##  In E0-MOT Position

[extruder]
step_pin: sb_can_th:PB3
dir_pin: sb_can_th:PA8
enable_pin: !sb_can_th:PA15

##  Update value below when you perform extruder calibration
##  If you ask for 100mm of filament, but in reality it is 98mm:
##  rotation_distance = <previous_rotation_distance> * <actual_extrude_distance> / 100
##  22.6789511 is a good starting point for Bondtech 5mm gears
##  34.37086 for Bondtech 8mm gears (Galileo)
rotation_distance: 22.6789511   #Bondtech 5mm Drive Gears
##  Update Gear Ratio depending on your Extruder Type
##  Use 50:17 for Afterburner/Clockwork (BMG Gear Ratio)
##  Use 80:20 for M4, M3.1
##  Use 7.5:1 for Galileo
gear_ratio: 50:10               #for Stealthburner/Clockwork2 BMG Gear Ratio
microsteps: 16
full_steps_per_rotation: 200    #200 for 1.8 degree, 400 for 0.9 degree
nozzle_diameter: 0.400
filament_diameter: 1.75
heater_pin: sb_can_th:PC15
## Check what thermistor type you have. See https://www.klipper3d.org/Config_Reference.html#common-thermistors for common thermistor types.
## Use "Generic 3950" for NTC 100k 3950 thermistors
sensor_type: Generic 3950
sensor_pin: sb_can_th:PA6
min_temp: 10
max_temp: 300
max_power: 1.0
min_extrude_temp: 170
#control = pid
#pid_kp = 26.213
#pid_ki = 1.304
#pid_kd = 131.721
##  Try to keep pressure_advance below 1.0
pressure_advance: 0.02
##  Default is 0.040, leave stock
pressure_advance_smooth_time: 0.040
max_extrude_cross_section: 50.0


[tmc2209 extruder]
uart_pin: sb_can_th:PA10
tx_pin: sb_can_th:PA9
interpolate: false
run_current: 0.7
sense_resistor: 0.110
stealthchop_threshold: 0
##diag_pin: sb_can_th:PB5
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

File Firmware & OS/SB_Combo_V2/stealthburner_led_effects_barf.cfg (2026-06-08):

# Macros for setting the status leds on the Voron StealthBurner toolhead (or for any neopixel-type leds).
#
# You will need to configure a neopixel (or other addressable led, such as dotstar). See
# https://www.klipper3d.org/Config_Reference.html#neopixel for configuration details.


#####################################
#           INSTRUCTIONS            #
#####################################
# How to use all this stuff:
#
#     1.  Copy this .cfg file into your Klipper config directory and then add [include stealthburner_leds.cfg]
#         to the top of your printer.cfg in order for register the LEDs and macros with Klipper.
#     2.  Define your LEDs by editing [neopixel sb_leds] below and entering the data pin from your control board
#         as well as the color order.
#
#           Note: RGB and RGBW are different and must be defined explicitly.  RGB and RGBW are also not able to 
#                 be mix-and-matched in the same chain. A separate data line would be needed for proper functioning.
#
#                 RGBW LEDs will have a visible yellow-ish phosphor section to the chip.  If your LEDs do not have
#                 this yellow portion, you have RGB LEDs.
#
#     3.  Save your config and restart Klipper.
#
#           Note: We set RED and BLUE to 1.0 to make it easier for users and supporters to detect 
#                 misconfigurations or miswiring. The default color format is for Neopixels with a dedicated 
#                 white LED. On startup, all three SB LEDs should light up.
#
#                 If you get random colors across your LEDs, change the color_order to GRB and restart. Then
#                 omit the W for each suggested color_order in the next paragraph.
#
#                 If you get MAGENTA, your  color order is correct. If you get CYAN, you need to use RGBW. If
#                 you get YELLOW, you need to use BRGW (note that BRG is only supported in the latest Klipper
#                 version).
#
#     4.  Once you have confirmed that the LEDs are set up correctly, you must now decide where you want 
#         these macros called up...which means adding them to your existing gcode macros.  NOTHING will happen
#         unless you add the STATUS_????? macros to your existing gcode macros.  
#
#           Example: add STATUS_LEVELING to the beginning of your QGL gcode macro, and then add STATUS_READY 
#                    to the end of it to set the logo LED and nozzle LEDs back to the `ready` state.
#
#           Example: add STATUS_CLEANING to the beginning of your nozzle-cleaning macro, and then STATUS_READY
#                    to the end of it to return the LEDs back to `ready` state.
#
#     5.  Feel free to change colors of each macro, create new ones if you have a need to.  The macros provided below
#         are just an example of what is possible.  If you want to try some more complex animations, you will most
#         likely have to use WLED with Moonraker and a small micro-controller (please see the LED thread for help inside
#         of the stealthburner_beta channel on Discord).
#
#####################################
#       END INSTRUCTRUCTIONS        #
#####################################


#[neopixel sb_leds]
#pin: PB0
#   The pin connected to the neopixel. This parameter must be provided.
#chain_count: 10
#   The number of Neopixel chips that are "daisy chained" to the
#   provided pin. The default is 1 (which indicates only a single
#   Neopixel is connected to the pin).
#color_order: GRB, GRB, GRB, GRB, GRB, GRB, GRB, GRB, GRBW,  GRBW
#   Set the pixel order required by the LED hardware. Options are GRB,
#   RGB, GRBW, or RGBW. The default is GRB.
#initial_RED: 1.0
#initial_GREEN: 0.0
#initial_BLUE: 1.0
#initial_WHITE: 0.0
#   Sets the initial LED color of the Neopixel. Each value should be
#   between 0.0 and 1.0. The WHITE option is only available on RGBW
#   LEDs. The default for each color is 0.#


##########################
# LED Effects Animations #
##########################

##################
## logo effects ##
##################

[led_effect sb_logo_busy]
autostart:              false
frame_rate:             24
leds:
    neopixel:sb_leds (1-8)
layers:
    breathing  3 1 top (1,0,0)

[led_effect sb_logo_cleaning]
autostart:              false
frame_rate:             24
leds:
    neopixel:sb_leds (1-8)
layers:
    breathing  3 1 top (0.0, 0.02, 0.5)

[led_effect sb_logo_calibrating_z]
autostart:              false
frame_rate:             24
leds:
    neopixel:sb_leds (1-8)
layers:
        breathing  3 1 top (0.0, 0.0, 0.35)

[led_effect sb_logo_heating]
leds:
    neopixel:sb_leds (1,3,7,8,6,2)
autostart:                          false
frame_rate:                         24
layers:
    comet  0.3  0 add (1, 0.18, 0)

[led_effect sb_logo_cooling]
leds:
    neopixel:sb_leds (1,3,7,8,6,2)
autostart:                          false
frame_rate:                         24
layers:
    comet  0.3  0 add (0, 0, 1)

[led_effect sb_logo_homing]
autostart:              false
frame_rate:             24
leds:
    neopixel:sb_leds (1-8)
layers:
        breathing  3 1 top (0.0, 0.6, 0.2)

[led_effect sb_logo_leveling]
autostart:              false
frame_rate:             24
leds:
    neopixel:sb_leds (1-8)
layers:
        breathing  3 1 top (0.5, 0.1, 0.4)

[led_effect sb_logo_meshing]
autostart:              false
frame_rate:             24
leds:
    neopixel:sb_leds (1-8)
layers:
        breathing  3 1 top (0.2, 1.0, 0.0)

[led_effect sb_logo_printing]
autostart:              false
frame_rate:             24
leds:
    neopixel:sb_leds (1-8)
layers:
    gradient  0.3  1 add (0.3, 0.0, 0.0),(0.3, 0.3, 0.0),(0.3, 0.1, 0.0)

[led_effect sb_logo_standby]
autostart:              false
frame_rate:             24
leds:
    neopixel:sb_leds (1-8)
layers:
        breathing  3 1 top (0.01, 0.01, 0.01)

[led_effect sb_logo_part_ready]
autostart:              false
frame_rate:             24
leds:
    neopixel:sb_leds (1-8)
layers:
        breathing  3 1 top (0.0, 1.0, 0.0)

####################
## nozzle effects ##
####################

[led_effect sb_nozzle_heating]
autostart:              false
frame_rate:             24
leds:
    neopixel:sb_leds (9,10)
layers:
        breathing  3 1 top (1.0, 0.18, 0.0, 0.0)

[led_effect sb_nozzle_cooling]
autostart:              false
frame_rate:             24
leds:
    neopixel:sb_leds (9,10)
layers:
        breathing  3 1 top (0.0, 0.0, 1.0, 0.1)

[led_effect sb_nozzle_standby]
autostart:              false
frame_rate:             24
leds:
    neopixel:sb_leds (9,10)
layers:
        breathing  3 1 top (0.6, 0.0, 0.0, 0.0)

[led_effect sb_nozzle_part_ready]
autostart:              false
frame_rate:             24
leds:
    neopixel:sb_leds (9,10)
layers:
        breathing  3 1 top (0.6, 1.0, 0.0, 0.1)


#####################
## all led effects ##
#####################

[led_effect sb_critical_error]
leds:
    neopixel:sb_leds
layers:
    strobe         1  1.5   add        (1.0,  1.0, 1.0)
    breathing      2  0     difference (0.95, 0.0, 0.0)
    static         1  0     top        (1.0,  0.0, 0.0)
autostart:                             false
frame_rate:                            24
run_on_error:                          true


[led_effect rainbow]
leds:
    neopixel:sb_leds
autostart:                          true
frame_rate:                         24
layers:
    gradient  0.3  1 add (0.3, 0.0, 0.0),(0.0, 0.3, 0.0),(0.0, 0.0, 0.3)


#######################
# LED Effects Statics #
#######################

[led_effect set_nozzle_leds]
leds:
    neopixel:sb_leds (9,10)
   #neopixel:caselight
autostart:                          false
frame_rate:                         24
layers:
    static         0  0     top        (0.0,  0.0, 0.0, 1.0)

[led_effect set_logo_leds]
leds:
    neopixel:sb_leds (1,2,3,4,5,6,7,8)
   #neopixel:caselight
autostart:                          false
frame_rate:                         24
layers:
    static         0  0     top        (1.0,  1.0, 1.0)

##############
# The Macros #
##############

[gcode_macro set_logo_leds_off]
gcode:
    SET_LED_EFFECT EFFECT=set_logo_leds STOP=1

[gcode_macro set_logo_leds_on]
gcode:
    SET_LED_EFFECT EFFECT=set_logo_leds

[gcode_macro set_nozzle_leds_on]
gcode:
    SET_LED_EFFECT EFFECT=set_nozzle_leds

[gcode_macro set_nozzle_leds_off]
gcode:
    SET_LED_EFFECT EFFECT=set_nozzle_leds STOP=1

[gcode_macro status_off]
gcode:
    STOP_LED_EFFECTS

[gcode_macro status_ready]
gcode:
    STOP_LED_EFFECTS
    SET_LED_EFFECT EFFECT=rainbow

[gcode_macro status_part_ready]
gcode:
    STOP_LED_EFFECTS
    SET_LED_EFFECT EFFECT=sb_nozzle_part_ready
    SET_LED_EFFECT EFFECT=sb_logo_part_ready

[gcode_macro status_busy]
gcode:
    STOP_LED_EFFECTS
    SET_LED_EFFECT EFFECT=sb_logo_busy
    set_nozzle_leds_on

[gcode_macro status_heating]
gcode:
    STOP_LED_EFFECTS
    SET_LED_EFFECT EFFECT=sb_logo_heating
    SET_LED_EFFECT EFFECT=sb_nozzle_heating
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

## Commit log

2024-02-20 Upload STLs
    Upload STLs
    [2020_Frame_Connector.stl, 2xJST_Holder[no_cut_fan_wires].stl, Chain_Anchor_3_Hole.STL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]
2024-02-24 Upload data
    Upload the wiring diagram and parameters
    [Five inches-Back plate x1.STL, Five inches-Front frame x1.STL, Five inches-Plug x1.STL]
2024-02-24 Upload BOM
    Upload BOM
2024-04-10 Updated STL
    Updated to correct version of Nevermore for Voron 2.4
    [v6_Cartridge_90deg.stl, v6_Cartridge_Straight.stl]
2024-05-24 add step file
    [VORON2.4_R2_PRO_Assembly.STEP]
2024-09-18 Wiring diagram update after replacing motherboard
2024-12-24 Update README.md
    Updated H7 Spider board link.
2025-03-14 Document Updates
    [Chain_Anchor_3_Hole_X.STL]
